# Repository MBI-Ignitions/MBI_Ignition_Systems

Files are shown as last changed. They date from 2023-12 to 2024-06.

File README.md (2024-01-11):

# Motorized Bike Ignition Systems by MBI

Welcome to the Motorized Bike Ignition Systems (MBI) repository! This open-source project aims to provide a comprehensive solution for motorized bike enthusiasts, offering a reliable and customizable ignition system.

## Table of Contents

- [Introduction](#introduction)
- [Features](#features)
- [Acquiring](#acquiring)
- [Updates](#updates)
- [License](#license)
- [Donate](#donate)
- [Contact](#contact)

## Introduction

Motorized Bike Ignition Systems (MBI) is an open-source project focused on developing high-quality ignition systems for motorized bikes. Our goal is the development of new CDI technology, tools for evaulating them, and providing open and closed source CDIs for motorized bike engines.

## Features

- **Reliability**: MBI ignition systems are designed for reliability, we overspec all parts and vet most of our designs before release for reliability.
- **Customization**: The project seeks to make it easy to custimize and modify the open-source designs for your own engines needs.
- **Compatibility**: Our ignitions are a drop in replacement for almost all stock motorized bike engines that use a standard magneto and magnet.
- **Open Source**: The entire project is open source, encouraging collaboration and innovation within the motorized bike community.

## Acquiring

There are a few ways you can go about acquiring a CDI. You can:
- Order your own boards (minimum of 5), components and equipment, then build them yourself. This is the cheapest option for small batches.
- Order your boards from an approved seller in your desired quantity, order components and equipment then build them yourself. This is cheaper for single board runs.
- Purchase a board and component kit (COMING SOON).
- Purchase a completed board. This is the easiest to get running out of the box.

## Updates

Since this is an open-source passion project, we are adding information when we find time to. The wiki will start to get more and more information as we build more testing equipment and gather more knowledge from the community. If you think that there's more to add then consider becoming a contributor or donating to the project!

## License
This project is licensed under the GPLv3 License. Feel free to use, modify, and distribute the designs in accordance with the terms outlined in the license.

## Donate
If you find this information helpful then consider contributing to the project! All donations go towards contributing to this repo and developing open source devices to add. 

<p align="center">
<a href="https://www.buymeacoffee.com/mbiignitions" target="_blank">Buy Me A Coffee</a>
</p>

## Contact
If have any questions then feel free to message us on facebook at Mbi Ignitions, or email us [here](mailto:mbiignitions@protonmail.com)

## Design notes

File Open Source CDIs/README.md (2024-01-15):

# Open Source CDIs
These CDIs have been pulled from online and transferred to modern circuit editing software.

## Table of Contents
- [Jaguar](#jaguar)
- [Baker](#baker)
- [Rohmell](#rohmell)
- [Design Principles](#designprinciples)

## Jaguar CDI
This is one of Jaguar's older designs, photos are openly found online. Credit to him on facebook here: https://www.facebook.com/michael.forrest.7798. Design is from [here](https://www.dragonfly75.com/motorbike/CDI/CDI-layout.jpg)
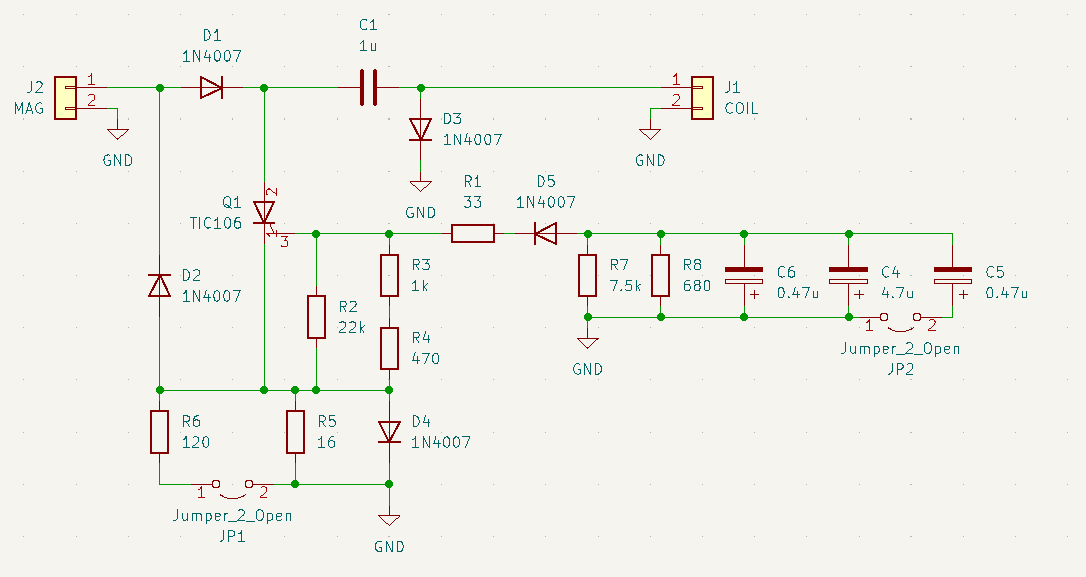
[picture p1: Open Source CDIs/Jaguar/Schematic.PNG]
Jaguar CDI Image


## Baker 
Jim Baker's design. This is his ultimate version with jumpers instead of a selector switch, and smaller 1N4007 diodes. Credit to him on facebook here: https://www.facebook.com/jim.baker.7927, he no longer builds them currently. 
One of his designs can be found online [here](https://www.blasterforum.com/media/zappy-cdi-coil-fired-adjustable-ignition.9499/full?d=1545531996)
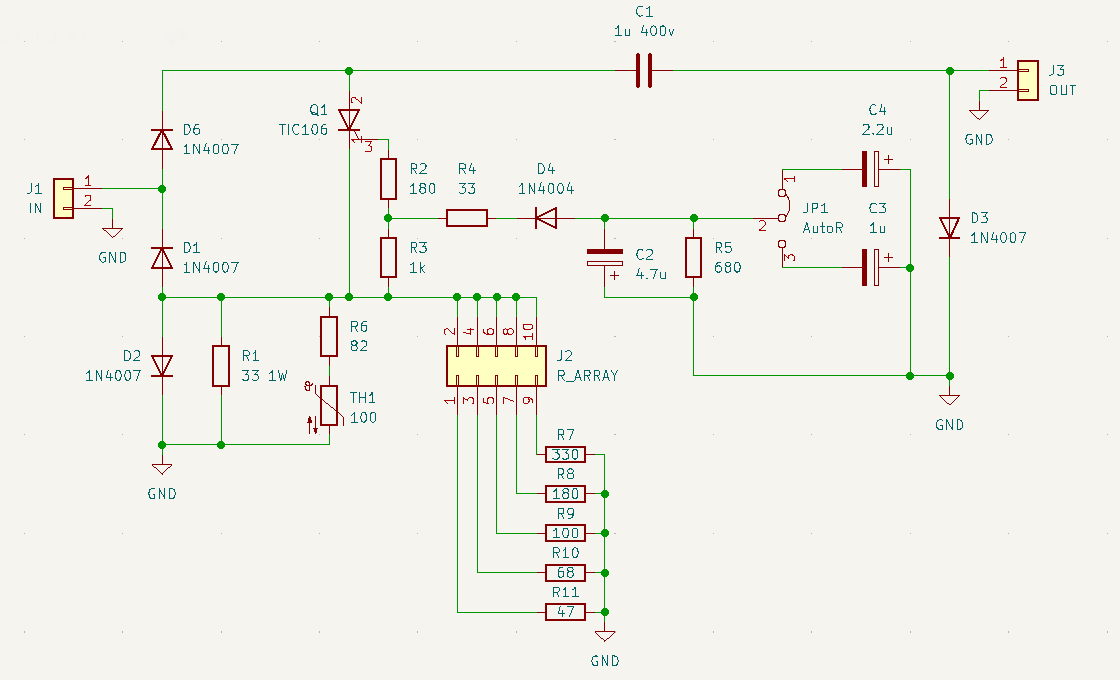
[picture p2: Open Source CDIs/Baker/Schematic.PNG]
Baker CDI Image


## Rohmell
Pulled from the motorized bike forum. Design can be found [here](https://www.google.com/url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)
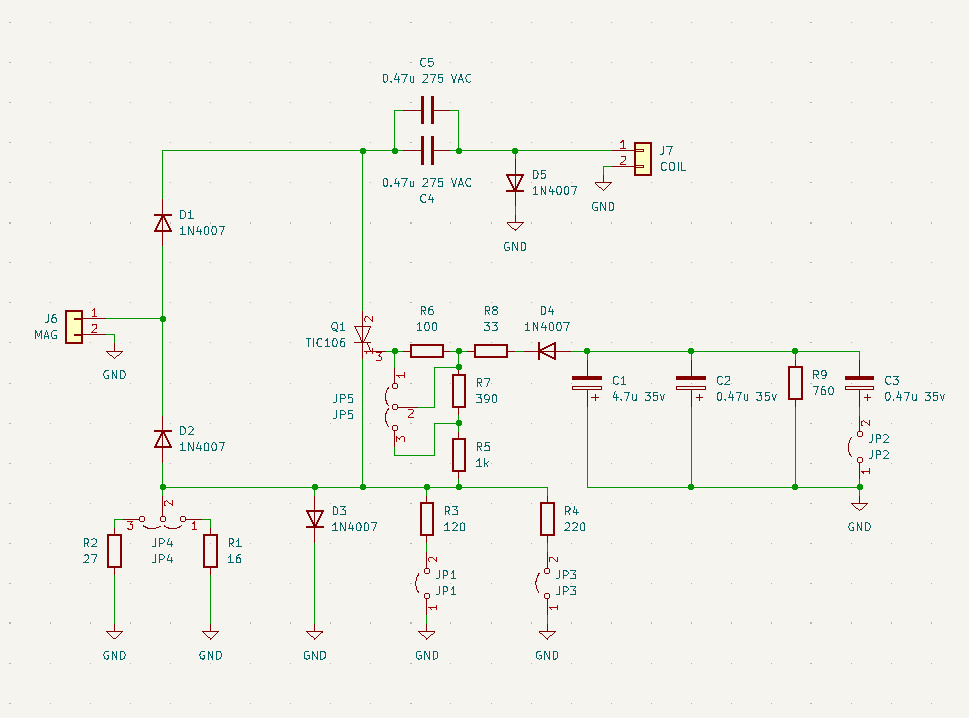
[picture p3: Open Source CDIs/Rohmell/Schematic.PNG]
Rohmell CDI Image


## DevPot (V1)
Our first open source development board designed in house. Uses potentiometers to control the resistance in critical areas, which allows for more adjustablility than other CDIs. Capacitance is changed by loading different capacitors into the push lock connectors.
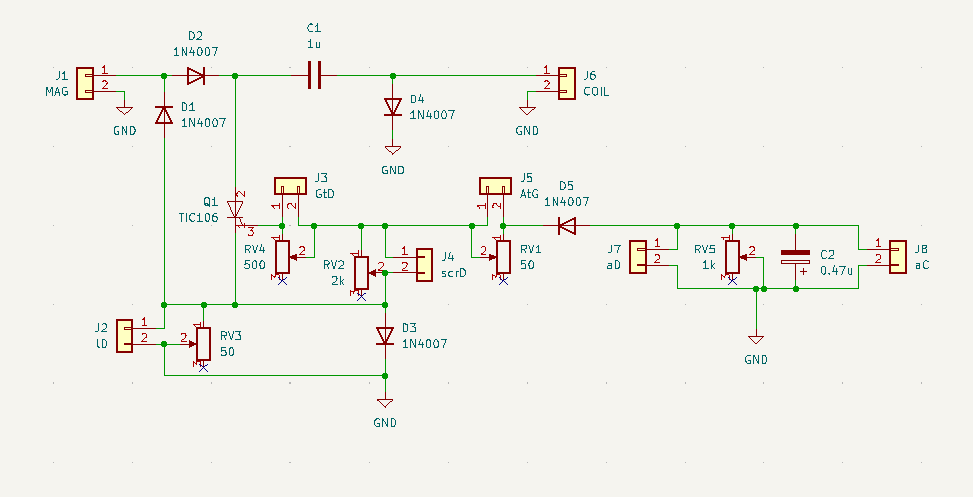
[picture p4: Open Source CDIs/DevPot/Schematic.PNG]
DevPot CDI Image


## DevPot V2
Identical to DevPot but with jumpers and a capacitor array to change the capacitance values.
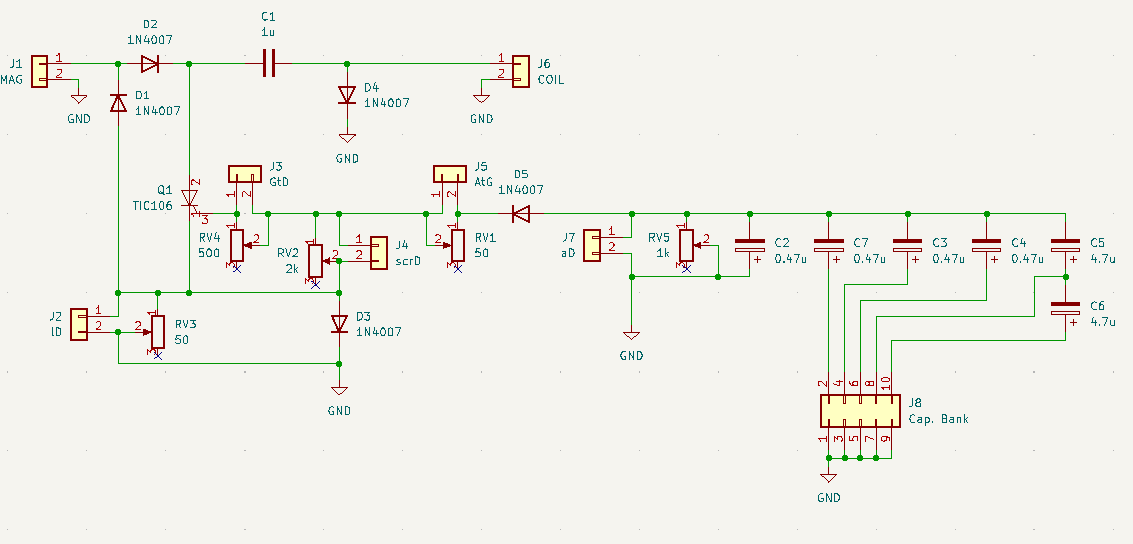
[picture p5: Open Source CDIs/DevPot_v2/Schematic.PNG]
DevPot CDI Image


## DevSnapLock
Our second open source development board with snap connectors for every value. This allows for the use of resistor packs instead of potentiometers, which are expensive. The capacitor bank is the same as DevPot with one connectors to load different capacitors.
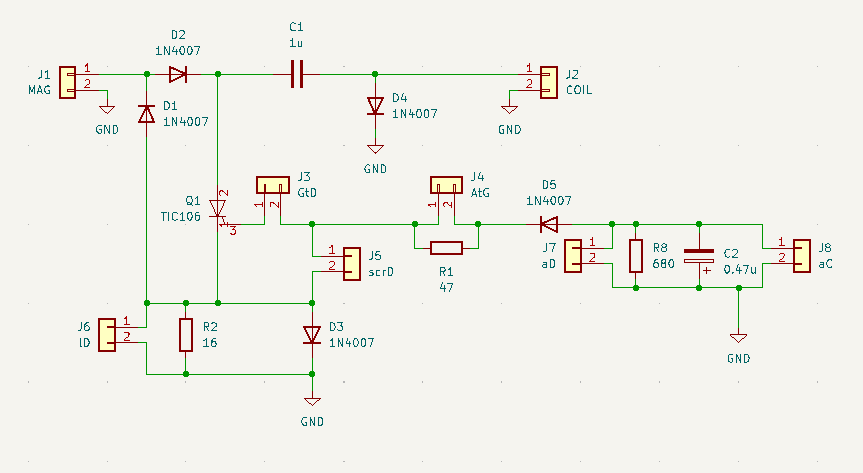
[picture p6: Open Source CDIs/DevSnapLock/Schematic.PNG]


## Design Principles
All of these designs follow the same principles:
- SCR to control the spark
- RC bank to control timing
- Diodes for rectification
- Resistor divider for further timing

Some designs also have themistors or thermal resistors. These are to change the timing depending the ambient temperature.

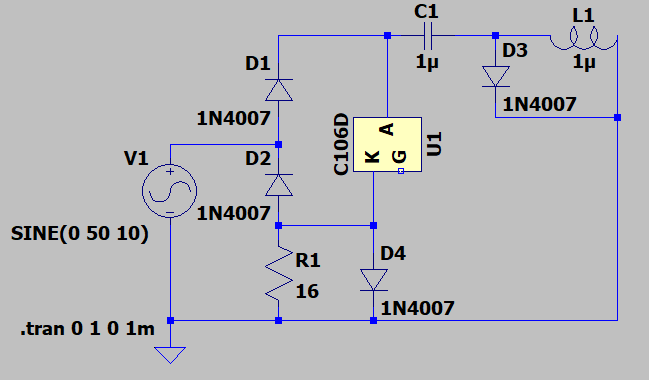
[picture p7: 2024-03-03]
Wiki/Images/CDINoTiming.PNG

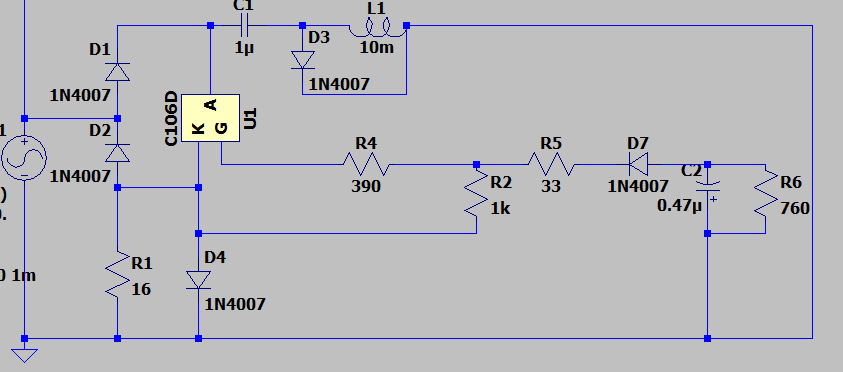
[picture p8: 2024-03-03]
Wiki/Images/CDITiming.PNG

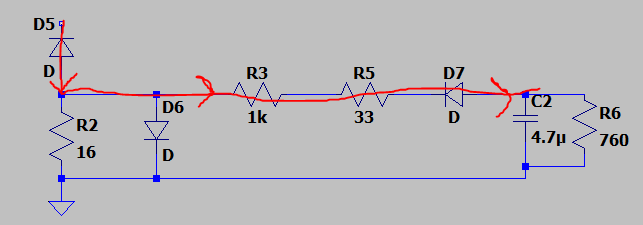
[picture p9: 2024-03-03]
Wiki/Images/CDITimingPath.PNG

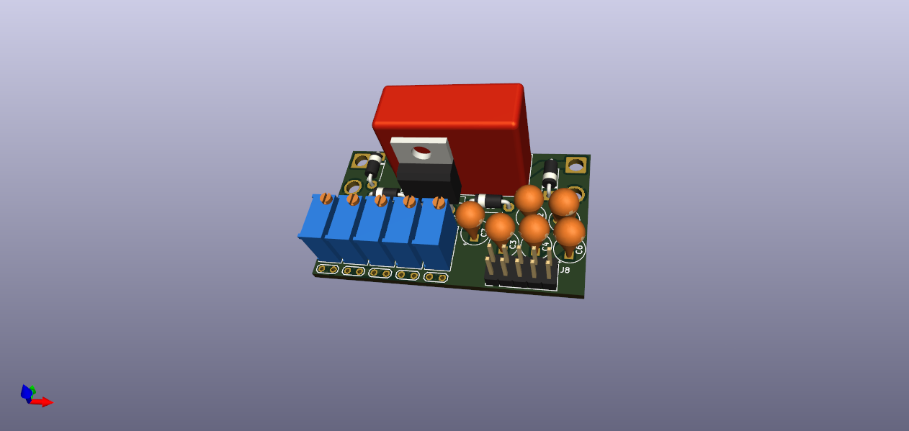
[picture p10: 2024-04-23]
Open Source CDIs/DevPot_v2/DevPot_v2.png

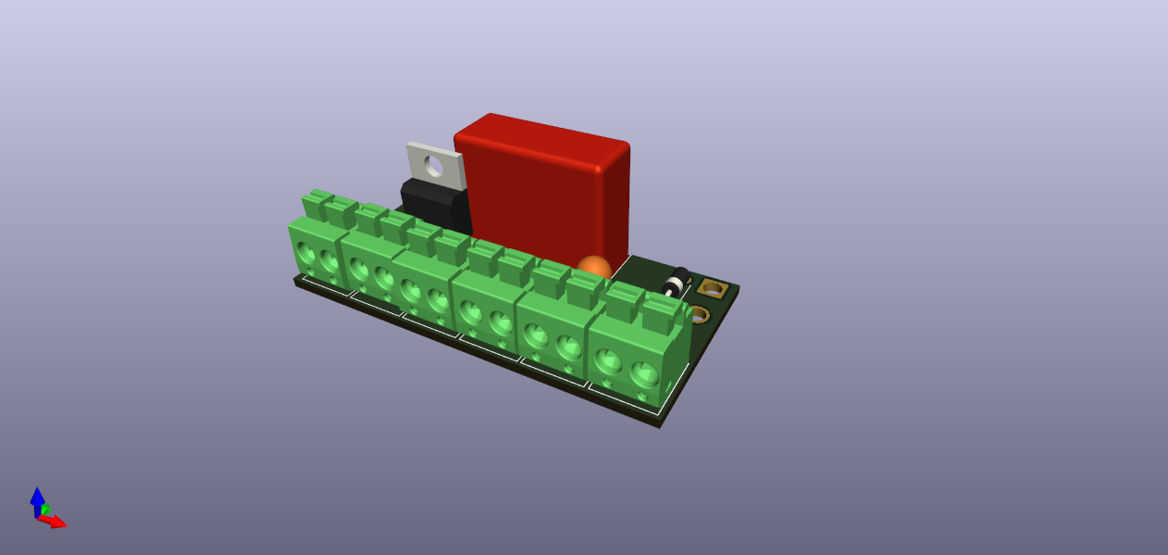
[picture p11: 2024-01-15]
Open Source CDIs/DevSnapLock/DevSnapLock.png

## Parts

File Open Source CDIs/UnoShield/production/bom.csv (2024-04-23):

Designator | Footprint | Quantity | Value | LCSC Part #
A2 | Arduino_Uno_R2_Shield | 1 | Arduino_Uno_R2_Shield
C1, C22 | C_Rect_L4.0mm_W2.5mm_P2.50mm | 2 | 10u
C10 | CP_Radial_D6.3mm_P2.50mm | 1 | 2.2u 400v
C11 | C_Rect_L4.0mm_W2.5mm_P2.50mm | 1 | 1u 35v
C15 | C_Rect_L4.0mm_W2.5mm_P2.50mm | 1 | 10u 16v
C18 | CP_Radial_D5.0mm_P2.00mm | 1 | 100u 10v
C2, C3 | C_Rect_L4.0mm_W2.5mm_P2.50mm | 2 | 1u
C30, C5, C8 | C_Rect_L4.0mm_W2.5mm_P2.50mm | 3 | 10n
C32 | C_Disc_D7.5mm_W5.0mm_P5.00mm | 1 | 22p 300v
C33 | C_Disc_D7.0mm_W2.5mm_P5.00mm | 1 | 1n 300v
C35 | C_Rect_L18.0mm_W8.0mm_P15.00mm_FKS3_FKP3 | 1 | 1u 400v
C4, C6 | C_Rect_L4.6mm_W3.0mm_P2.50mm_MKS02_FKP02 | 2 | u1
D1, D10, D11, D4, D6 | D_DO-41_SOD81_P7.62mm_Horizontal | 5 | 1N4007
D12, D3 | D_DO-41_SOD81_P7.62mm_Horizontal | 2 | 1N5819
D13, D14, D15 | D_DO-35_SOD27_P7.62mm_Horizontal | 3 | 1N5231B
D2 | D_DO-15_P10.16mm_Horizontal | 1 | SA5.0A-TP
D5, D7, D8 | LED_D5.0mm | 3 | LED
D9 | D_DO-41_SOD81_P7.62mm_Horizontal | 1 | 1N4937
J3 | PinSocket_1x02_P2.54mm_Vertical | 1 | KILL
J4 | SolderWire-1.5sqmm_1x02_P6mm_D1.7mm_OD3mm | 1 | MAG
J5 | SolderWire-1.5sqmm_1x02_P6mm_D1.7mm_OD3mm | 1 | CDI
L1 | L_Radial_D8.7mm_P5.00mm_Fastron_07HCP | 1 | 3300uH
Q3 | TO-220-3_Vertical | 1 | TIC106
R10 | R_Axial_DIN0207_L6.3mm_D2.5mm_P7.62mm_Horizontal | 1 | 2.94k 1%
R12 | R_Axial_DIN0207_L6.3mm_D2.5mm_P7.62mm_Horizontal | 1 | 680
R18 | R_Axial_DIN0207_L6.3mm_D2.5mm_P7.62mm_Horizontal | 1 | 100
R21 | R_Axial_DIN0207_L6.3mm_D2.5mm_P7.62mm_Horizontal | 1 | 10k
R23 | R_Axial_DIN0309_L9.0mm_D3.2mm_P12.70mm_Horizontal | 1 | 476.4k
R24 | R_Axial_DIN0309_L9.0mm_D3.2mm_P12.70mm_Horizontal | 1 | 3.6k
R25, R28 | R_Axial_DIN0207_L6.3mm_D2.5mm_P7.62mm_Horizontal | 2 | 1k
R27 | R_Axial_DIN0207_L6.3mm_D2.5mm_P7.62mm_Horizontal | 1 | 27
R4 | R_Axial_DIN0309_L9.0mm_D3.2mm_P12.70mm_Horizontal | 1 | 470
R5, R6, R7 | R_Axial_DIN0207_L6.3mm_D2.5mm_P7.62mm_Horizontal | 3 | 220
R8 | R_Axial_DIN0207_L6.3mm_D2.5mm_P7.62mm_Horizontal | 1 | 2k 1%
RV1 | Potentiometer_Bourns_3296Y_Vertical | 1 | 100k
SW1 | SW_PUSH_6mm | 1 | SW_Push
TP1 | PinHeader_1x01_P2.54mm_Vertical | 1 | VREF
TP2 | TestPoint_Pad_2.0x2.0mm | 1 | GATE_OUT
U2 | PowerIntegrations_PDIP-8C | 1 | LNK3206D

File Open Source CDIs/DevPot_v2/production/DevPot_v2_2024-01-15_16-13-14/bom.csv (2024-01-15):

Designator | Footprint | Quantity | Value | LCSC Part #
C1 | C_Rect_L26.5mm_W10.5mm_P22.50mm_MKS4 | 1 | 1u
C2, C3, C4, C7 | CP_Radial_Tantal_D5.5mm_P2.50mm | 4 | 0.47u
C5, C6 | CP_Radial_Tantal_D5.5mm_P2.50mm | 2 | 4.7u
D1, D2, D3, D4, D5 | D_DO-41_SOD81_P7.62mm_Horizontal | 5 | 1N4007
J1 | SolderWire-2.5sqmm_1x02_P7.2mm_D2.4mm_OD3.6mm | 1 | MAG
J2 | TestPoint_2Pads_Pitch2.54mm_Drill0.8mm | 1 | lD
J3 | TestPoint_2Pads_Pitch2.54mm_Drill0.8mm | 1 | GtD
J4 | TestPoint_2Pads_Pitch2.54mm_Drill0.8mm | 1 | scrD
J5 | TestPoint_2Pads_Pitch2.54mm_Drill0.8mm | 1 | AtG
J6 | SolderWire-2.5sqmm_1x02_P7.2mm_D2.4mm_OD3.6mm | 1 | COIL
J7 | TestPoint_2Pads_Pitch2.54mm_Drill0.8mm | 1 | aD
J8 | PinHeader_2x05_P2.54mm_Vertical | 1 | Conn_02x05_Odd_Even
Q1 | TO-220-3_Vertical | 1 | TIC106
RV1, RV3 | Potentiometer_Bourns_3296W_Vertical | 2 | 50
RV2 | Potentiometer_Bourns_3296W_Vertical | 1 | 2k
RV4 | Potentiometer_Bourns_3296W_Vertical | 1 | 500
RV5 | Potentiometer_Bourns_3296W_Vertical | 1 | 1k

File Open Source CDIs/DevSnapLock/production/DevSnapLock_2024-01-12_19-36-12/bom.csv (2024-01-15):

Designator | Footprint | Quantity | Value | LCSC Part #
C1 | C_Rect_L26.5mm_W10.5mm_P22.50mm_MKS4 | 1 | 1u
C2 | CP_Radial_Tantal_D5.5mm_P2.50mm | 1 | 0.47u
D1, D2, D3, D4, D5 | D_DO-41_SOD81_P7.62mm_Horizontal | 5 | 1N4007
J1 | SolderWire-2.5sqmm_1x02_P7.2mm_D2.4mm_OD3.6mm | 1 | MAG
J2 | SolderWire-2.5sqmm_1x02_P7.2mm_D2.4mm_OD3.6mm | 1 | COIL
J3 | TE_1792863 | 1 | GtD
J4 | TE_1792863 | 1 | AtG
J5 | TE_1792863 | 1 | scrD
J6 | TE_1792863 | 1 | lD
J7 | TE_1792863 | 1 | aD
J8 | TE_1792863 | 1 | aC
Q1 | TO-220-3_Vertical | 1 | TIC106
R1 | R_Axial_DIN0207_L6.3mm_D2.5mm_P7.62mm_Horizontal | 1 | 47
R2 | R_Axial_DIN0207_L6.3mm_D2.5mm_P7.62mm_Horizontal | 1 | 16
R8 | R_Axial_DIN0207_L6.3mm_D2.5mm_P7.62mm_Horizontal | 1 | 680

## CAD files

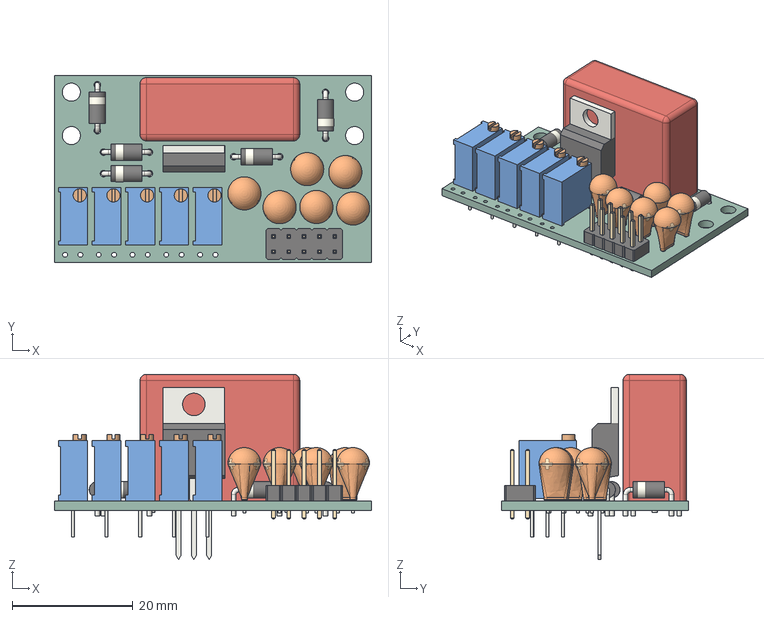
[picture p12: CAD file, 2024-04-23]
Open Source CDIs/DevPot_v2/DevPot_v2.step
52.6 x 31.0 x 30.8 mm
DevPot_v2 PCB

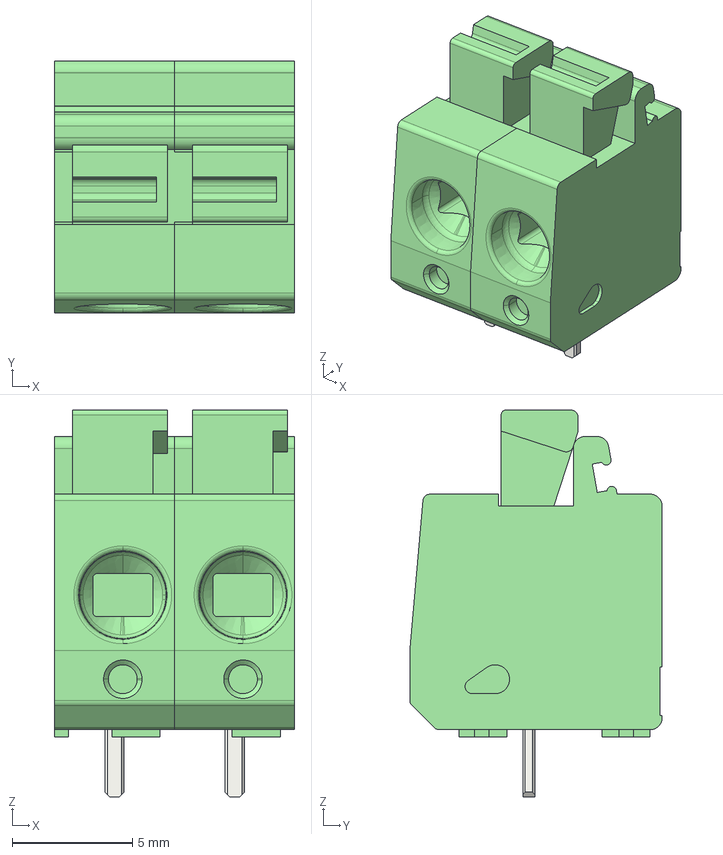
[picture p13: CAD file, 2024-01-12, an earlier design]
Open Source CDIs/DevPot/1792863.step
10.00 x 10.5 x 16.1 mm

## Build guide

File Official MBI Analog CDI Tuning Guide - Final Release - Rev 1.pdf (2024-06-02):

## Official MBI Analog CDI Tuning Guide

### Written by Sean Davis - Revision 1

## Analog CDI - MK2.2M

All MK2.2M CDIs come pre-adjusted and pre-wired for bolt on “plug and play” operation. The MK2.2M CDI was originally adjusted for “mostly stock” 2 stroke ‘Motorized Bicycle Kit’ engines. It has also been tested on numerous configurations of “performance modified” 2 stroke ‘Motorized Bicycle Kit’ engines. This testing demonstrated improved performance with the “out of the box” settings when compared to all the commonly available “non-adjustable” ‘Performance Ignitions’ available across the Motorized Bicycle Industry.

Any major engine modification like aftermarket heads, aftermarket ‘Expansion Chamber’ exhaust systems, cylinder port map modification, switching to Race Gas from Pump Gas, etc. may require adjustment of the ignition timing curve in order to achieve the full performance potential of the modifications. The following is a guideline for adjusting the Analog MK2.2M CDI. Perform adjustments in the order given below.

Any change to any component in the complete “Ignition Path” (magneto, magnet, coil or plug) will have an effect on the resulting ignition curve with the SAME CDI settings. The ignition curve images presented within this document were all recorded using “stock” Avenger85 Magneto and Magnet; OEM Honda CR80 Ignition Coil; and NGK XR5IX Spark Plug.

## Section 1: Wiring Instructions

The MK2.2M CDI comes pre-wired with the correct terminals for “plug and play” operation. There are 2 pairs of wires that exit the CDI’s 3d printed case. Both pairs of wires are 1x red wire and 1x black wire. One pair of wires is terminated with “Double Female Bullet Connectors”. This pair of “Double Female Bullet Connectors” is wired to the Magneto AND to the Kill Switch if installed. The white Magneto wire is left unused. The other pair of wires is terminated as follows: 1x black wire terminates in a “Loop Terminal”, 1x red wire terminates in a “Female Blade Connector”. This pair of “Loop Terminal” and “Female Blade Connector” is wired to the included Ignition Coil that came with the MK2.2M CDI.

The connections are as follows (Kill Switch is Optional):

MK2.2M CDI - Black - Double Female Bullet → Stock Magneto - Black - Male Bullet MK2.2M CDI - Red - Double Female Bullet → Stock Magneto - Red (or Blue) - Male Bullet MK2.2M CDI - Black - Double Female Bullet → Kill Switch - Green - Male Bullet
MK2.2M CDI - Red - Double Female Bullet → Kill Switch - Yellow w/Green - Male Bullet MK2.2M CDI - Black - Loop Terminal → Ignition Coil - Ground Post (-) - Secured with Bolt/Nut MK2.2M CDI - Red - Female Blade → Ignition Coil - Positive (+) - Male Blade

## Section 2: Tuning Method

If you already know the exact timing curve your engine requires, then you will need a “Timing Light” and some form of ‘TDC/Timing Degree Indicator’. In this case, you will not be “tuning” the CDI, but instead merely “setting” the CDI to the pre-determined ideal timing curve that has -already- been “tuned” for the engine. In this case, the timing light is REQUIRED to confirm the actual timing curve output from the ’Adjustable CDI’ matches exactly the pre-determined ideal timing curve. As this is a “Tuning Guide”, it will NOT focus on this method of “setting” the CDI to some pre-determined set of absolute values.

If you DO NOT already know the exact timing curve your engine requires, then you do not necessarily need a “Timing Light” and some ‘TDC/Timing Degree Indicator’. In this case, you will be “tuning” the CDI to determine what settings result in the most ideal timing curve for your engine.

This guide will focus on detailing a method for “tuning” the CDI in very much the same fashion as you would “tune” a carburetor. For example: An Air-to-Fuel Ratio (AFR; Lambda) Sensor (O2 Sensor) is not necessarily required to properly “tune” a carburetor. Observation of how the engine responds to changes in carburetor settings provides sufficient feedback to the tuner to determine the required “jetting” for a specific engine and carburetor combination.

The most basic method followed to “tune” a carburetor is to “sweep” a range of adjustment for each individual “circuit” in the carburetor from “too rich” to “too lean”. It is advisable to start “too rich” because this is “safe” for the engine. **Running the engine with a “too lean” setting can result in permanent damage to the engine**. As the adjustment is “swept” from being too rich to the “lean” direction; at each step: Engine response is evaluated, and various methods for monitoring the engine for “overheating” are employed. A good tuner will “read” the tell-tale signs on the spark plug and the crown of the piston for signs of being “too lean”. Each circuit in the carburetor is successively “swept” in this manner, starting from the lowest RPM range (idle circuit) to the highest RPM range (main jet circuit). The adjustment settings that result in “best” engine performance and “safe” piston crown/spark plug temps is the “correct jetting” for the engine.

This guide will follow the same basic principles. The user will “tune” the CDI by “sweeping” the range of adjustment for each individual “adjustable value” in the CDI from “too retarded” to “too advanced”. It is advisable to start “too retarded” because this is “safe” for the engine. **Running the engine with a “too advanced” setting can result in permanent damage to the engine**. As the adjustment is “swept” from being too retarded to the “advanced” direction; at each step: Engine response is evaluated, and various methods for monitoring the engine for “overheating” are employed. A good tuner will “read” the tell-tale signs on the spark plug and the crown of the piston for signs of being “too advanced”. Each tunable value in the CDI is successively “swept” in this manner, starting from the lowest RPM range (Initial Advance) to the highest RPM range (Retard Curve). The adjustment settings that result in “best” engine performance and “safe” piston crown/spark plug temps is the “correct timing” for the engine.

## Section 3: Initial Advance (Base Timing)

Adjustable Value = Potentiometer “RV1” Stock Value = 16 Ohms
Effective Range = 10 – 40 Ohms

Initial Advance or “Base Timing” will affect the entire timing curve equally. Adjusting this value will not significantly change the “shape” of the curve, but instead will change every single point along the curve by the same amount. Increasing the value (higher Ohms) will “lift” the entire timing curve by 1 degree for every 1 Ohm of increase. Decreasing the value (lower Ohms) will “drop” the entire timing curve by 1 degree for every 1 Ohm of decrease. Adjusting this value is the same as using an off-set woodruff key (timing key) or a timing plate to advance/retard the physical position of the Magneto Rotor Magnet relative to the Magneto Stator Coil.

The stock value of 16 Ohms should be “safe” for most engine combinations when using a stock crankshaft and magnet with standard woodruff keys (NOT off-set). To determine the ideal value for your engine, it is advised to connect the MK2.2M CDI following the instructions from ‘Section 1: Wiring Instructions’ and to run the engine using the stock “out of the box” values.

**This first “run test” is ideally done with a brand-new spark plug of the appropriate heat range and with a carburetor “tune” that is close to ideal**

The engine should be run long enough to come up to operating temperature and if the engine is responding favorably to the stock settings at least 1-3 WOT runs should be completed. If the engine is NOT responding favorably to the stock settings (wont rev, hard starting, pinging/knocking, etc.) then shut the engine down immediately.

After the first “run test” has been completed with the stock “out of the box” values, the spark plug should be removed and evaluated. The most important indicator for timing analysis is what is referred to as the “timing mark” (see: Section 6: Tips and Tricks; ‘How to Read a Spark Plug’). Evaluate the location of the “timing mark” on the ‘ground strap’ of the spark plug to determine how much timing is optimal for your engine. If the “timing mark” is burned all the way down to the shell/first thread of the spark plug then there is TOO MUCH timing and RV1 should be adjusted DOWN. If the “timing mark” has not yet burned past the mid-point of the “J-Strap/ Ground Strap” of the spark plug then there is NOT ENOUGH timing and RV1 should be adjusted UP.

This will be your STARTING POINT for the ‘Adjustable Value’ “RV1”. The next sections of the tuning guide will detail a method for tuning the SHAPE of the timing curve. After adjusting the SHAPE of the timing curve, it may be necessary to “re-tune” the Initial Advance/ Base Timing again to ensure “best” engine performance AND “safe” piston crown/spark plug temps across the entire RPM range.

## Example Curves – Adjusting RV1:

-as measured with Avenger85 Stock Magneto Stator and Magnet

-Magnet installed in “advanced” position

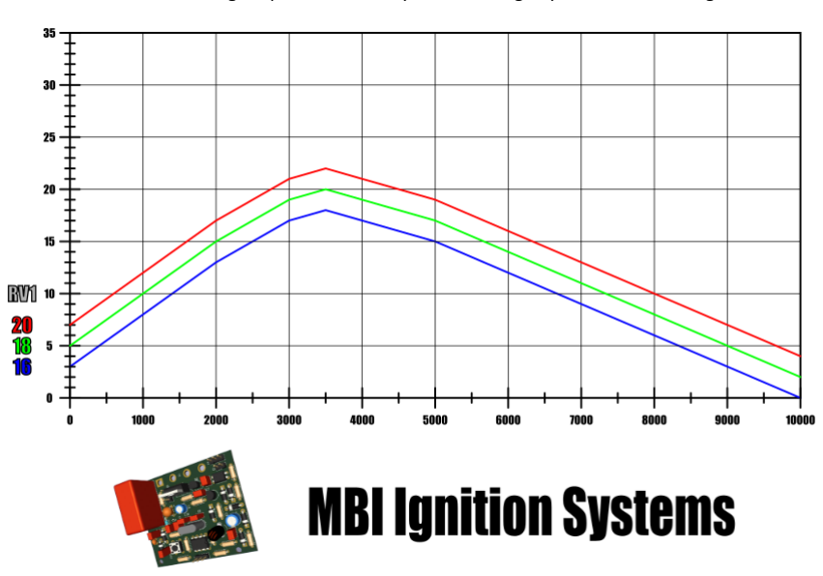
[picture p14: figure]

-Installed magnet position can vary “Base Timing” by as much as 10 degrees

## Section 4: Curve Peak (Crossover Point)

Adjustable Value = Potentiometer “RV3” Stock Value = 760 Ohms
Effective Range = 350 – 950 Ohms

The “curve” created by the MK2.2M CDI can be imagined as a simple “bell curve”. At 0 RPM the timing value is very low. From 0 RPM’s, the curve will “advance” as RPM’s rise, up to a peak at a specific RPM. The adjustable value “RV3” controls at what RPM the “peak” of this timing curve occurs. After the “Curve Peak”, ignition timing begins to “retard” back the other direction as RPM’s continue to rise.

Thus, RV3 controls the specific RPM of the “Crossover Point” between the “rising” section of the timing curve and the “falling” section of the timing curve. Increasing the value (higher Ohms) will “shift” the Crossover Point ~250 RPM’s lower for every ~100 Ohms of increase. Decreasing the value (lower Ohms) will “shift” the Crossover Point ~250 RPM’s higher for every ~100 Ohms of decrease.

The ideal RPM for this “Crossover Point” will be determined mostly by the RPM where the engine makes peak torque and (if fitted with one) the resonant frequency of the expansion chamber exhaust. A higher peak Torque RPM/ higher pipe resonant frequency will favor a higher RPM “Crossover Point”.

The stock value of 760 Ohms should be “safe” for most engine combinations to start with. This will result in a “Crossover Point” at ~3,500 RPM with the stock 5.17 uF Capacitance value. To determine the ideal value for your engine, it is advised to REDUCE the value of “RV3” in ~100 Ohm steps and test the engine. At each step: evaluate the response of the engine and examine the spark plug for signs of over-heating/ too much timing advance. Continue testing in this manner until “best” engine performance with “safe” piston crown/spark plug temps are obtained.

After adjusting this “Crossover Point” of the timing curve to the ideal value, it may be necessary to “re-tune” the Initial Advance/ Base Timing (“RV1”) again to ensure “best” engine performance AND “safe” piston crown/spark plug temps across the entire RPM range.

## Example Curves – Adjusting RV3:

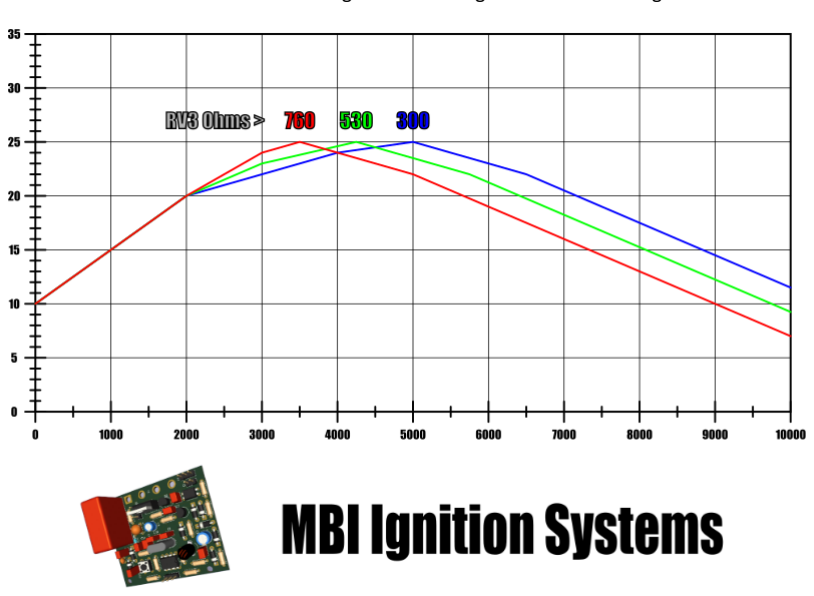
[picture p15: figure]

-as measured with Avenger85 Stock Magneto Stator and Magnet

## Section 5: Retard Curve (Shape)

Adjustable Value = “Capacitor Bank” Stock Value = 5.17 uF
Effective Range = 0.47 – 5.64 uF

The “falling” section of the timing curve (also called the “Retard Curve”) will affect the “tail” of the timing curve; everything AFTER the “Curve Peak/ Crossover Point”. Increasing the value (higher Capacitance) will “pull” the retard curve down more sharply as RPM’s rise. Decreasing the value (lower Capacitance) will “pull” the retard curve down less sharply as RPM’s rise.

Adjusting the capacitance value WILL influence the “Crossover Point” RPM. Lower Capacitance will “shift” the “Crossover Point” to a higher RPM. A 0.47 uF change in capacitance will “shift” the “Crossover Point” up/down about ~400 RPM. Because of this, any change to the Capacitance Value of the “Capacitor Bank” will require an adjustment of RV3 to restore the ideal “Crossover Point” RPM that was determined in Section 4: Curve Peak (Crossover Point).

The ideal “shape” for this “Retard Curve” will be determined mostly by the design of the combustion chamber within the head. A slower burning head will need more ignition advance and thus will favor lower capacitance values that do not pull timing as sharply. A faster burning head will need less ignition advance and thus will favor higher capacitance value that pull timing more sharply.

The stock value of 5.17 uF should be “safe” for most engine combinations to start with. To determine the ideal value for your engine, it is advised to REDUCE the value of the “Capacitor Bank” in ~0.47 uF steps and test the engine. Every time Capacitance is changed, the value of RV3 should be adjusted to restore the ideal “Crossover Point” RPM that was determined in Section 4: Curve Peak (Crossover Point). Each 0.47 uF reduction in Capacitance should require a ~200 Ohm increase to the value of RV3 to restore the ideal “Crossover Point” RPM. At each step: evaluate the response of the engine and examine the spark plug for signs of over-heating/ too much timing advance. Continue testing in this manner until “best” engine performance with “safe” piston crown/spark plug temps are obtained.

After adjusting the “Retard Curve” to the ideal capacitance value AND restoring the ideal “Crossover Point” RPM (“RV3”), it may be necessary to “re-tune” the Initial Advance/ Base Timing (“RV1”) again to ensure “best” engine performance AND “safe” piston crown/spark plug temps across the entire RPM range.

## Example Curves – Adjusting Capacitance:

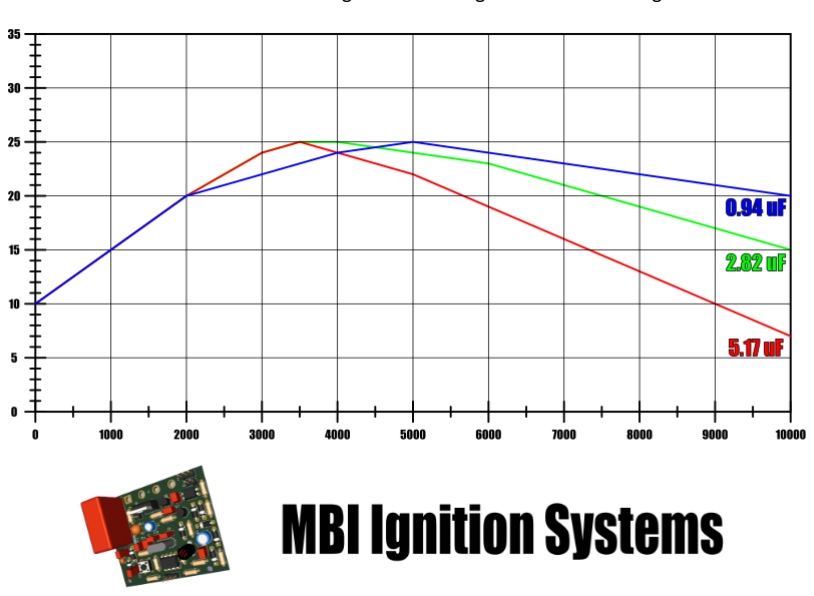
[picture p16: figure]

-as measured with Avenger85 Stock Magneto Stator and Magnet

## Section 6: Tips and Tricks

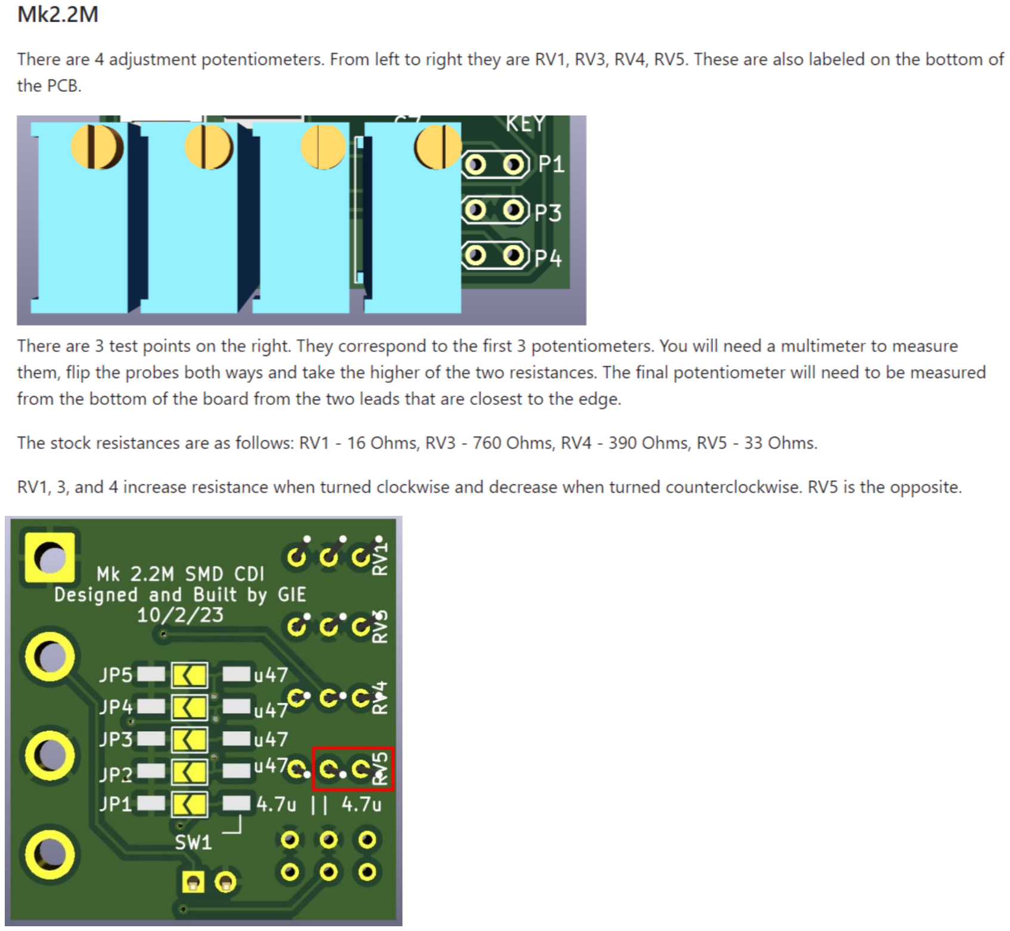
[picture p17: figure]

MK2.2M Analog CDI Turn – to – Ohms:

- RV1 = ~1/2 turn = 1 Ohm
- RV3 = ~2 1/2 turns = 100 Ohms
- RV4 = ~2 1/2 turns = 50 Ohms
- RV5 = ~1/2 turn = 1 Ohm

How to read a Spark Plug:

The spark plug's strap, also known as the ignition timing mark, has two marks on a 90-degree bend that indicate the base timing and the total timing. The first mark is the base timing, and the second mark is the total timing. The strap will burn a color change in these two spots. If the strap is burned all the way down to the base thread, it has too much timing. If the strap burns all the way down to the middle of the band, it has too little timing. The strap will burn cleaner as you add timing to it. The base of the strap is usually a good spot for peak torque and horsepower.

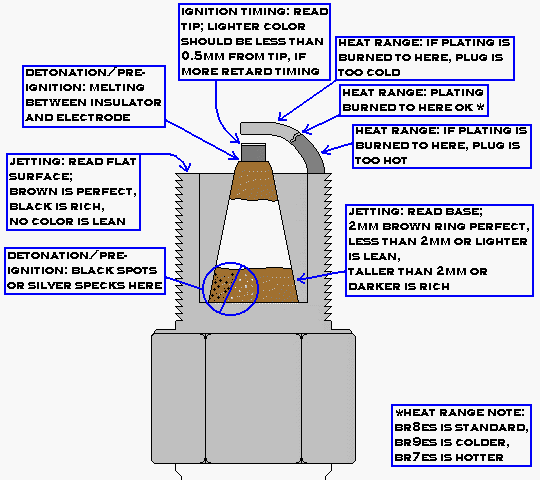
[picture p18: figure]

How to read Piston Crown:

The piston crown on a perfectly tuned engine will have a faint “wash pattern” burnt on to it. This “wash pattern” is the result of the oil in the 2-stroke pre-mix burning hot enough to turn to carbon and “stick” to the aluminum surface of the piston crown. As the piston crown gets hotter and hotter on the way to “overheating” this wash pattern will become a deeper and deeper black, and will encroach out to the edges of the piston, eventually covering the entire piston crown in an even layer of black soot. This is not yet truly over-heated, but it is hotter than ideal. As the piston is run hotter and hotter, this deep black soot will start to lighten, becoming an “ashy” gray color. This will start in a small circle at the very center of the piston crown. When you can see the “ashy” gray color begin to form on the top-side of the piston, you are VERY CLOSE to burning a hole right through the piston crown. If you start to see the “ashy” gray circle form in the center of your piston crown or on the exhaust edge of the piston, you can be 100% sure you are over-heating your piston. If the carburetion is known to be “good” then this is most likely caused by TOO MUCH ignition advance.

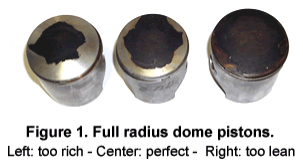
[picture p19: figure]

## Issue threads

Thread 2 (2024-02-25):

Discrepency Between Block Diagram Labels and Tuning Page "Stock Settings" Values

exokinetic, 2024-02-25:
Firstly, I would like to thank you for making this project public and open source under GPL liscence!

Secondly, I would like to thank you for sharing your research with regards to the block diagrams from the "previous art" CDI's that have been available to us up until now.

Thirdly, I would like to thank you sharing the circuit design principles so that others can follow along with the work!

Before I dive into the juicier details of the actual circuit design, and EXACTLY what is going on within;

I believe there are a few typo's between the block diagram and the tuning page, allow me to explain....

---------------------------------------------------------------------------------------------------------------------------------------------------

RV1 has a "stock value" of 16 Ohms.

RV1 is a 0-50 Ohm Pot on the DevPot V2 Block Diagram.

There is a 33 Ohm Resistor in the Jaguar CDI Block Diagram at exactly that location.

The images on your tuning page come from the Jaguar dragonfly45.com website.

The "16 Ohm" Pot is the one that is adjusted to move the whole curve up/down 1 degree per 1 Ohm of value change.

+1 Ohm on the 16 Ohm (stock setting) Pot should yield +1 Deg for EVERY step on the curve, based on the image you have on the "tuning" page which is following the JAGUAR CDI design principles; as the image is coped directly from his website.

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

The 16 Ohm Pot is on ONE SIDE of the "Voltage Divider" (you call it a 'resistor divider', but technically its called a VOLTAGE divider, and the distinction is important, as it explains why it effects the entire curve by the same amount)

Which side of the voltage divider the "higher resistance" is on is quite important in the effect it has on the voltage passing through it, as the equation for the voltage divider is thus:

V(out) = V(in)*((R2/(R1+R2))

Where R1 is on the "positive"/ "voltage source" side of V(out) and R2 is on the "negative"/"ground path" side of V(out).

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

As you can see, unless R1 is exactly equal to R2, it matter's what side its on.  This is called the "Resistor Ratio" of the "Voltage Divider".

In the Jaguar CDI Block Diagram the 16 Ohm resistor is in the "RV3" position of the DevPot V2 Block Diagram, NOT the RV1 position.

The DevSnapLock Block Diagram appears to CORRECT this error, placing the 16 Ohm SnapLock resistor in the exact same position as the Jaguar CDI.  Now called the R2 position on the DevSnapLock Block Diagram, and would correspond to the "RV3" position of the DevPot V2 Block Diagram.

Can you please confirm the location of the "16 Ohm Stock Setting Potentiometer" for the DevPot V2 design?

Is it INDEED in the RV1 position?

Or is that a typo, and its actually RV3 that is the "16 Ohm Stock Setting Potentiometer" (which would match the Jaguar CDI design)

---------------------------------------------------------------------------------------------------------------------------------------------------

RV3 has a "stock value" of 760 Ohms.

RV3 is a 0-50 Ohm Pot on the DevPot V2 Block Diagram.

There is a 16 Ohm Resistor in the Jaguar CDI Block Diagram at exactly that location.

How -exactly- do you set a 0-50 Ohm Pot to 760 Ohms?!

This is clearly a typo somewhere.

The most likely "correct" labeling/ stock settings in my opinion is that RV3 is -ACTUALLY- the "16 Ohm" stock setting position.

There are only -TWO- Potentiometer's in the DevPot V2 Block Diagram that are OVER 0-500 Ohm Pots.

RV2 is labeled as a 1k Pot
RV5 is labeled as a 1k Pot

Based on on the fact that the Jaguar CDI has a 680 Ohm Resistor in the RV5 position, I think it is most likely that "760 Ohm" is the stock setting for RV5, and NOT RV3.

Can you confirm exactly what is correct here, as it is not possible that RV3 has a stock setting of 760 Ohms.

---------------------------------------------------------------------------------------------------------------------------------------------------

RV4 has a "stock value" of 390 Ohms.

RV4 is a 0-500 Ohm Pot on the DevPot V2 Block Diagram.

There is a 470 Ohm Resistor in the Jaguar CDI Block Diagram right around that position.

This actually seems correct.

Can you please confirm that this is correct?

---------------------------------------------------------------------------------------------------------------------------------------------------

RV5 has a "stock value" of 33 Ohms.

RV5 is a 0-1000 Ohm Pot on the DevPot V2 Block Diagram.

Why a 0-1000 Ohm Pot if the stock value is so low...?

There is a 7.5k and a 680 Ohm Resistor in the Jaguar CDI Block Diagram at exactly that location.

There is also a 33 Ohm Resistor in the Jaguar CDI Block Diagram at exactly the RV1 position on the DevPot V2 Block Diagram.

It seems MUCH more likely that RV1 should have the "stock value" of 33 Ohms and that RV5 should have the "stock value" of 760 Ohms.

Can you confirm exactly what is correct here?

---------------------------------------------------------------------------------------------------------------------------------------------------

Image for Reference:

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

I am excited to begin discussing the actual design of the circuit, and what adjusting the various resistor/ capacitor locations should do to the resulting spark curve, and WHY that happens based on basic circuit design principles.  Ohm's Law, Farraday's Law, Len's Law, etc, etc.

Thank you again!

-Sean Davis

jephilp, 2024-03-03:
I'll do my best to answer all your questions here, I'll be adding images as well for clarity sake.

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

Here is the schematic for the CDI, I have also added it to the respective tuning section.

To start, you got fairly close in figuring out what the actual schematic with labeling was which I applaud and is very impressive! I did _purposely_ change a lot of the designators to obscure them from people looking to copy my designs, but since this appears to now be an issue it is time that I release the schematic to make everyone's life easier.

This should answer your questions as you can see they are not typos, just me referencing the schematic directly without showing it. If it is still confusing to have them all different we can look at changing ALL the designs to have a common reference designator between them.

exokinetic, 2024-03-04:
> To start, you got fairly close in figuring out what the actual schematic with labeling was which I applaud and is very impressive!

You left JUST enough clues!

And I will admit to being a sucker for a good puzzle.

I have very much enjoyed the process.

>If it is still confusing to have them all different we can look at changing ALL the designs to have a common reference designator between them.

So long as the tuning page matches what you actually get in the mail, it shouldnt cause too much confusion.

I dont know how many others "need" the benefit of the wiring block diagram...

But, I would absolutely support "unifying" the labelling convention used across the diagrams!

Thanks again!

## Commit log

2023-11-08 Added Archive
    Adding older designs and creating an archive for them. All of these designs are experimental, please build at your own risk and give credit if you are creating a fork.
    [Mk1CDI.kicad_pcb, Mk1CDI.kicad_sch, Mk1CDIs.kicad_pcb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]
2023-12-18 Added 3 new cdis
    Added Jaguar, Rohmell and Baker cdis to the open source directory. Readmes will be added soon.
    [Baker.kicad_pcb, Baker.kicad_sch, Jaguar.kicad_pcb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]
2023-12-22 Added PNGs of schematics
2024-01-11 Updated READMEs
    Added credit to all current cdis and made some tweaks
2024-01-12 Added DevPot and DevSnapLock
    Added two new development boards that are based on changing the different values of a CDI.
    [1792863.step, DevPot.kicad_pcb, DevPot.kicad_sch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]
2024-01-15 Added new CDIs and updated README
    Added the DevPot_v2 CDI, updated the readme to include all of the new CDIs and included images for each. Also add production exports for all the boards.
    [1792863.step, DevPot.kicad_pcb, DevPot_v2.kicad_pcb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]
2024-04-23 April Updates!
    - Created and add the first open source digital CDI!
    - Made some tweaks and updates to the other open source analog CDIs
    - Cleaned up the backup files
    [DevPot_v2.step, bom.csv, designators.csv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]
